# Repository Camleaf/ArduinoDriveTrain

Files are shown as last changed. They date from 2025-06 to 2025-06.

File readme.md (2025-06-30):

# Three wheel Crab drivetrain

**Description:** This robot can move in any direction without turning, using the Crab drive motion. It is controlled with the attached controller joysticks with the left joystick for arcade movement relative to the heading, and the right joystick to control the heading.

**Motivation:** I did this project because I wanted a challenge, also because I am looking towards joining an FRC team for the first time next year, and I wanted to make a drivetrain inspired by some robots I saw there. This project ended up taking less time than I anticipated (mostly because I was putting in 7-8 hour days on it), but it was still very fun.

**File Layout**:
 - **CAD**: contains the STEP files for the entire built, imports and all
 - **FIRMWARE**: contains all the code put on the microcontrollers
 - **WIRING**: Contains fritzing file, breadboard view and schematic view images, for both the controller and the car
 - **PRODUCTION**: Contains the individual .3mf files which will be 3D printed
 - **JOURNALIMG**: Where I store all the images I used for my journal

### Car Design Images

NOTE: The motors at the bottom of the design will get their power through wires from the motor drivers which are routed via the two big holes in each of the layers of design. Since to motors only move 90 degrees in either direction from their starting point in this design, the wires will never get tangled.

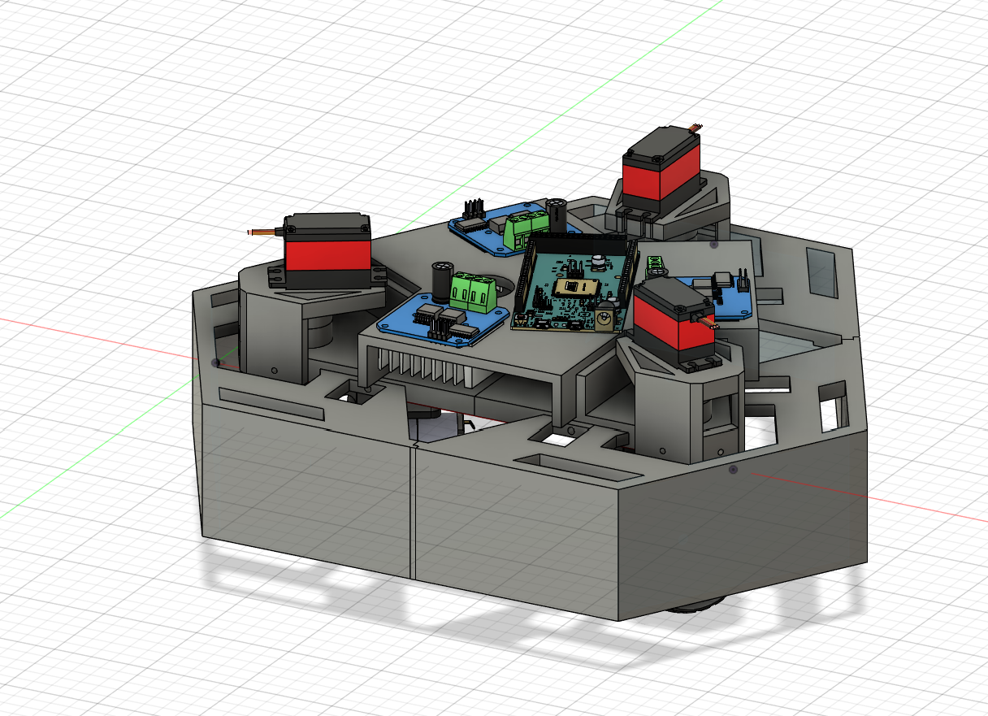
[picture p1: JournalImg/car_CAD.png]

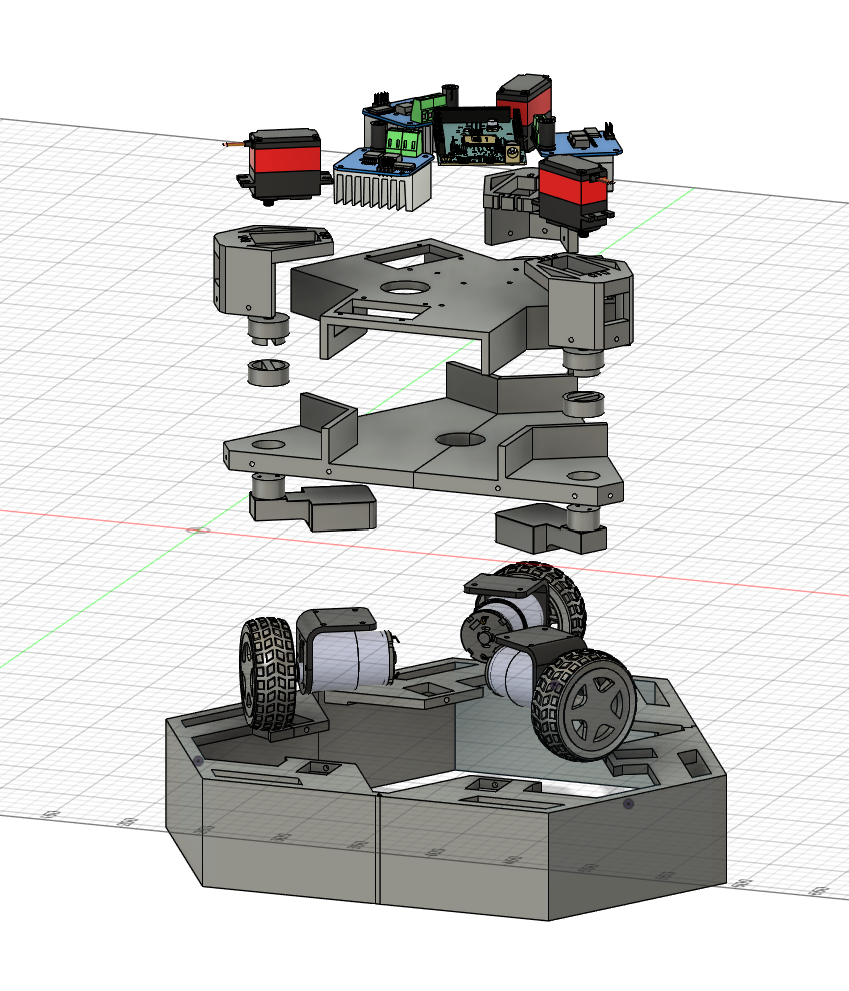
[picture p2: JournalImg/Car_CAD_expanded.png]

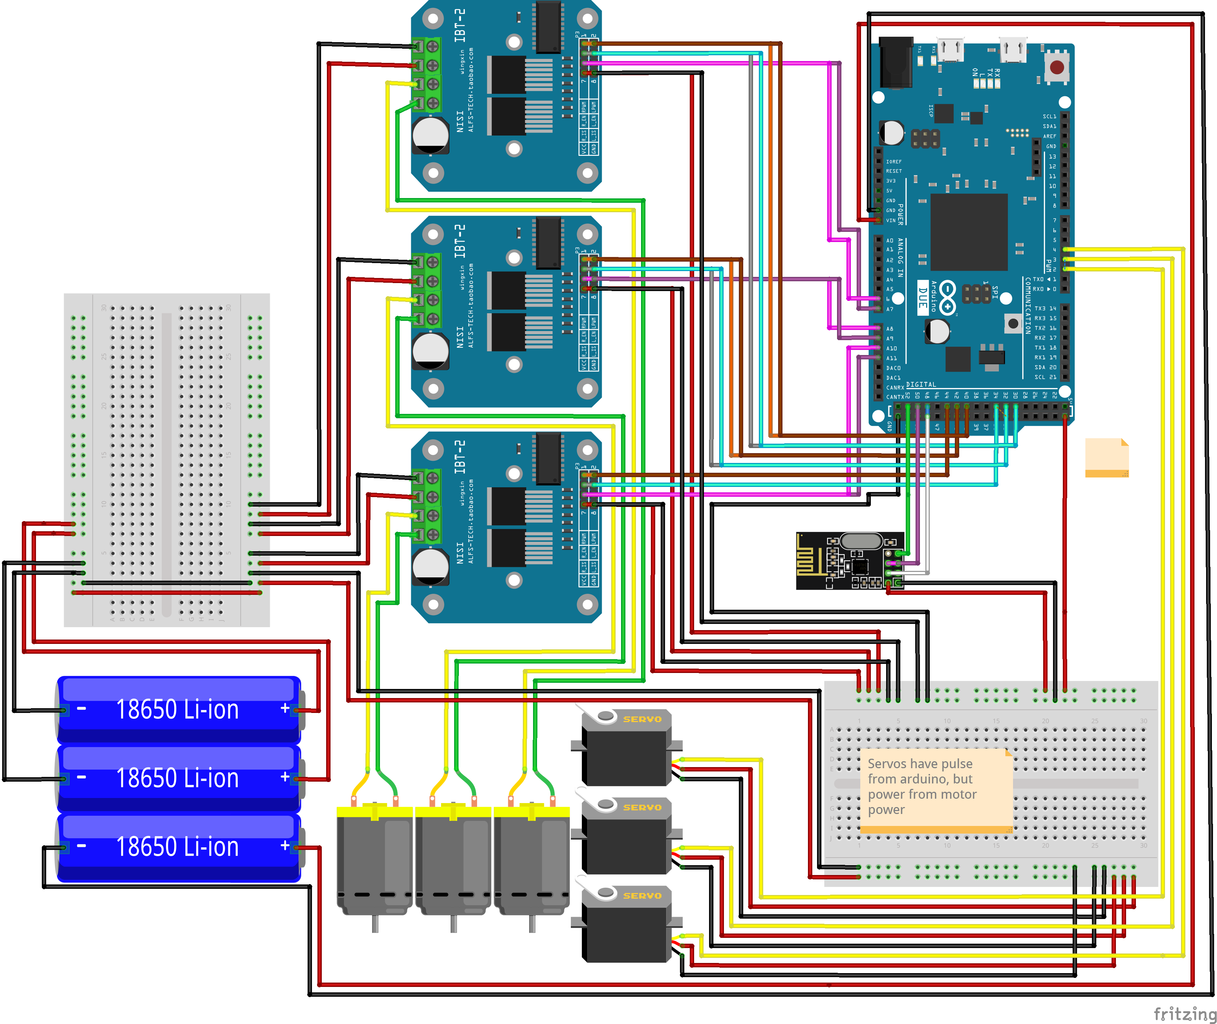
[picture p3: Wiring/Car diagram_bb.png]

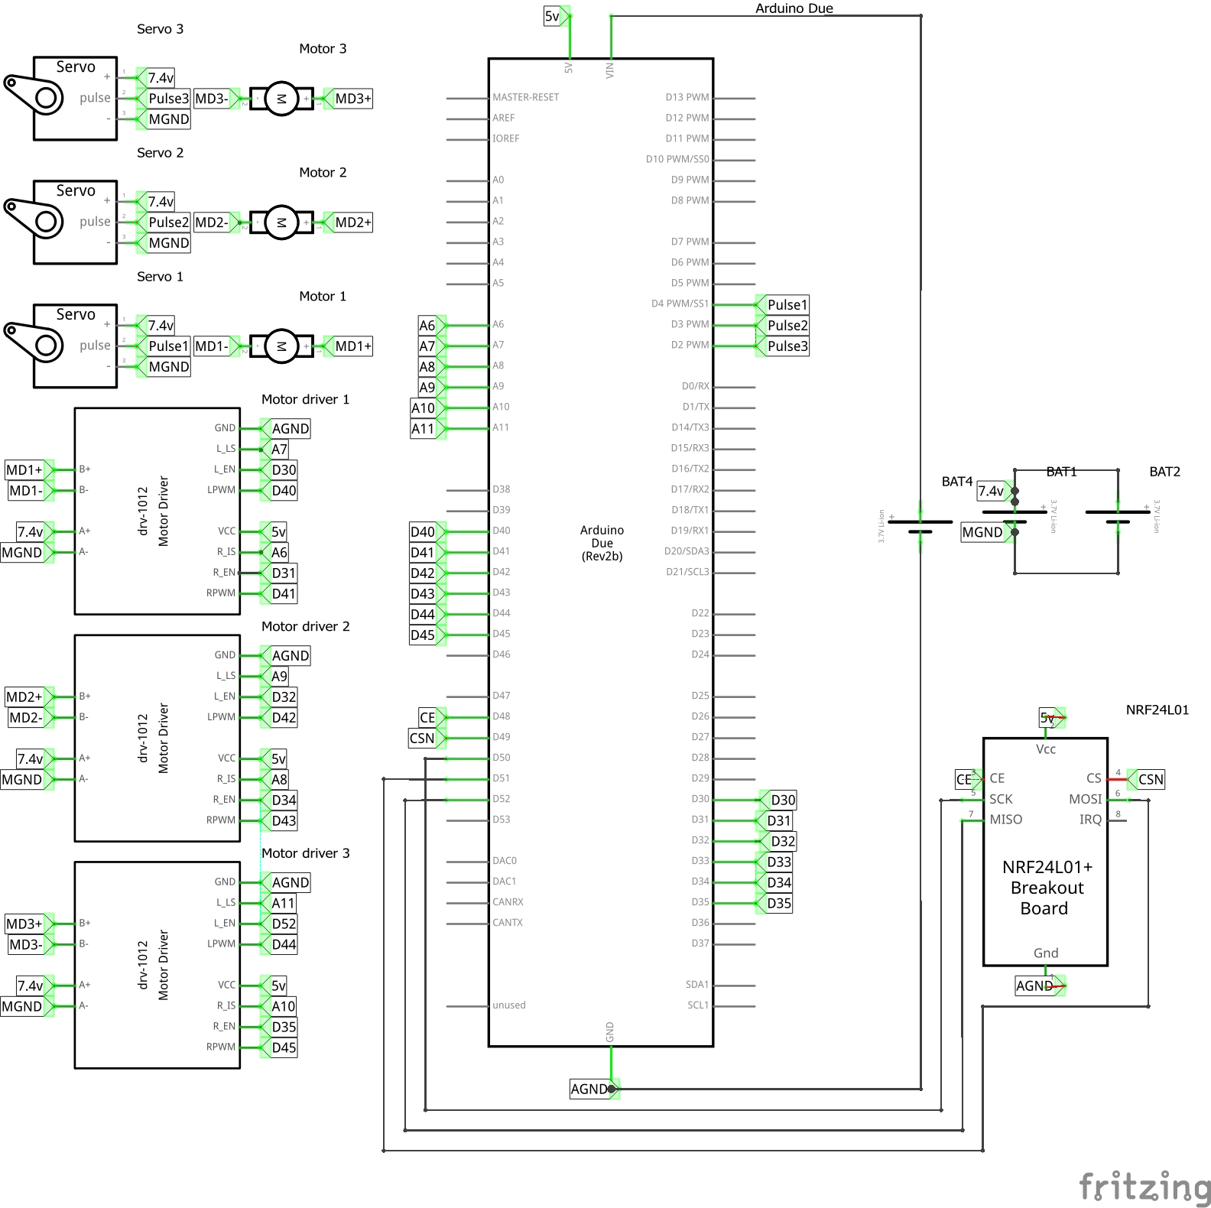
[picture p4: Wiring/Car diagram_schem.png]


### Controller Design Images

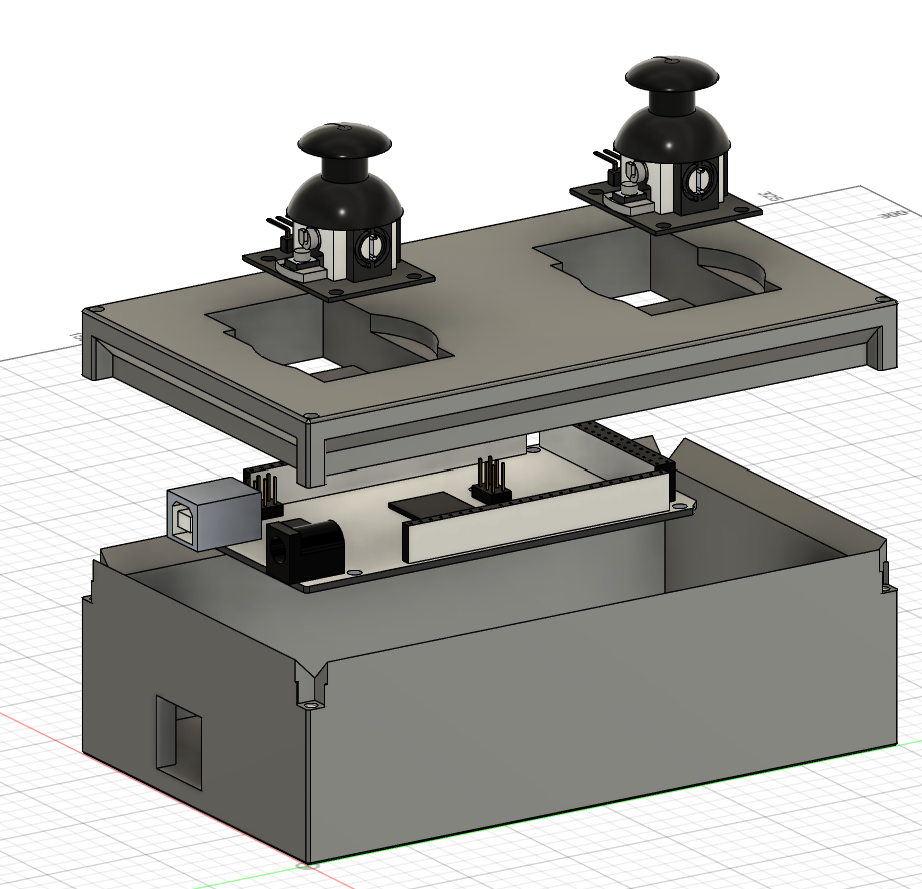
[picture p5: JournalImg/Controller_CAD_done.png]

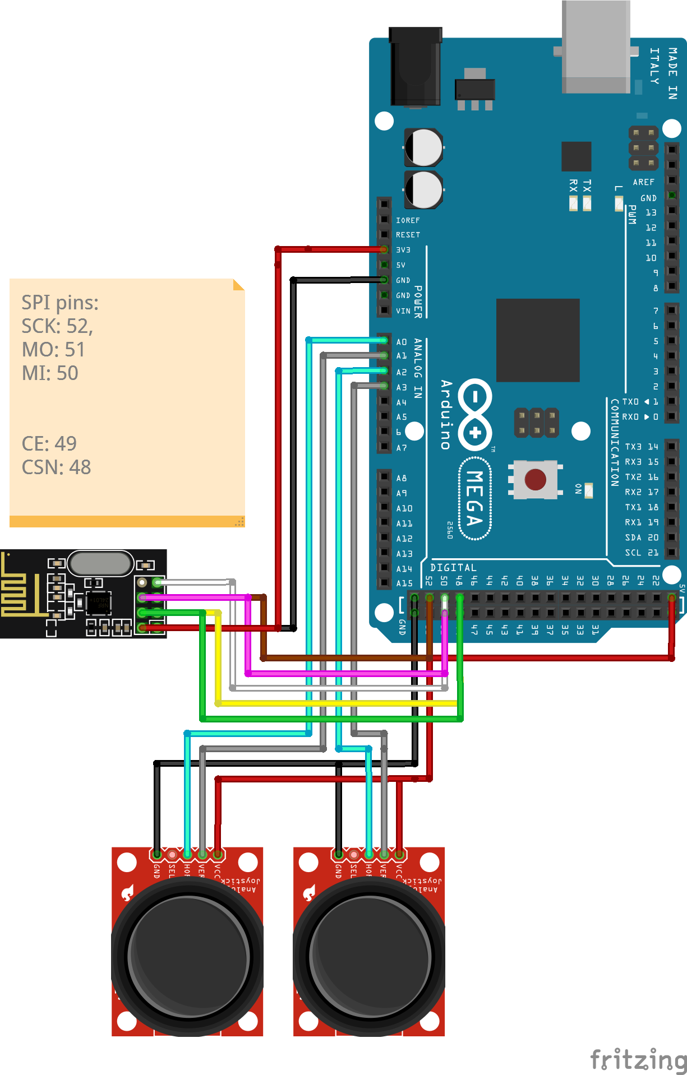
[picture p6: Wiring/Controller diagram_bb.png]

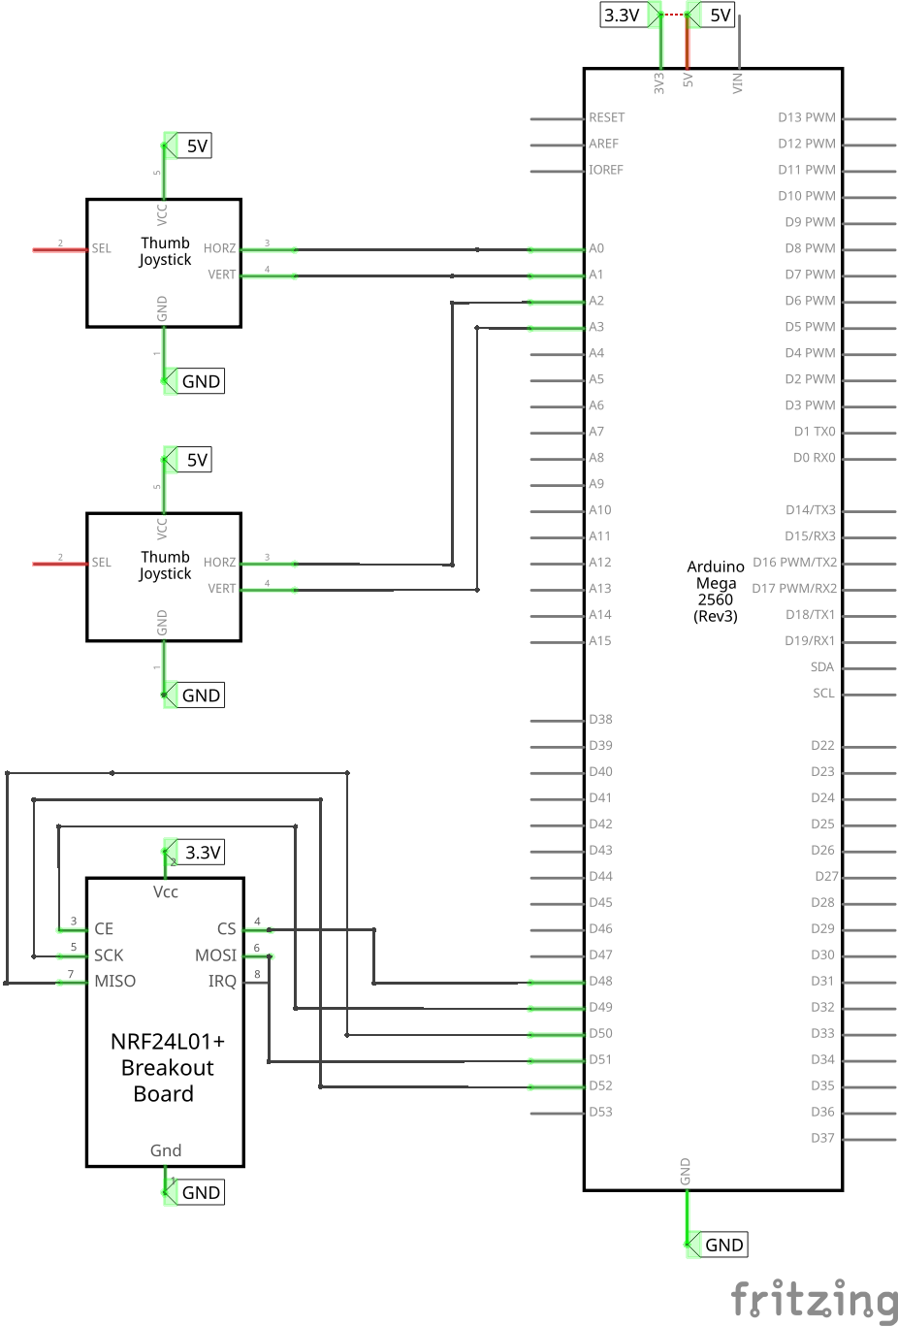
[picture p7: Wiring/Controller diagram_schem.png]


### BOM

I have a lot of parts at home and 3D printing capabilities so this list is just what I don't have.

|Item #|Name |Quantity|Type |Description |Cost |Link |FIELD8|FIELD9|FIELD10|
|---|---|---|---|---|-----|---|---|---|---|
|1 |BTS7960 |2 |2pcs |Motor Driver |6.04 |https://www.aliexpress.com/item/1005006795884033.html?spm=a2g0o.cart.0.0.37ee38dastskZr&mp=1 | | | |
|2 |XY joystick |1 |5pcs |Joystick for controller |3.21 |https://www.aliexpress.com/item/1005009059629265.html?spm=a2g0o.cart.0.0.37ee38dastskZr&mp=1 | | | |
|3 |7.4v 1500mAh battery pack|1 |3pcs charger |Powers motors/servos |11.29|https://www.aliexpress.com/item/1005007104046547.html?spm=a2g0o.cart.0.0.37ee38dastskZr&mp=1 | | | |
|4 |JGB37 DC motor |4 |6V bracket motor|main motors |16.63|https://www.aliexpress.com/item/1005009003269281.html?spm=a2g0o.cart.0.0.37ee38dastskZr&mp=1 | | | |
|5 |Arduino Mega |1 |official-cable  |microprocessor |12.99|https://www.aliexpress.com/item/1005006661386732.html?spm=a2g0o.cart.0.0.37ee38dastskZr&mp=1 | | | |
|6 |JX PDI-6221mg servos |1 |4pc |servos to rotate motor  |16.63|https://www.aliexpress.com/item/32880168203.html?spm=a2g0o.cart.0.0.37ee38dastskZr&mp=1 | | | |
|7 |USB power bank |1 |1pc |Power for microprocessor|10.71|https://www.aliexpress.com/item/1005008829680504.html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| | | |
| |Shipping |N/A |N/A |N/A |36.47| |

Total: $129.92 USD

With tax: $146.8096 USD

This is with Aliexpress First time shopper welcome sales, as I have never shopped there before.
The previous total was ~$180. Good thing those exist so I could get under the limit.

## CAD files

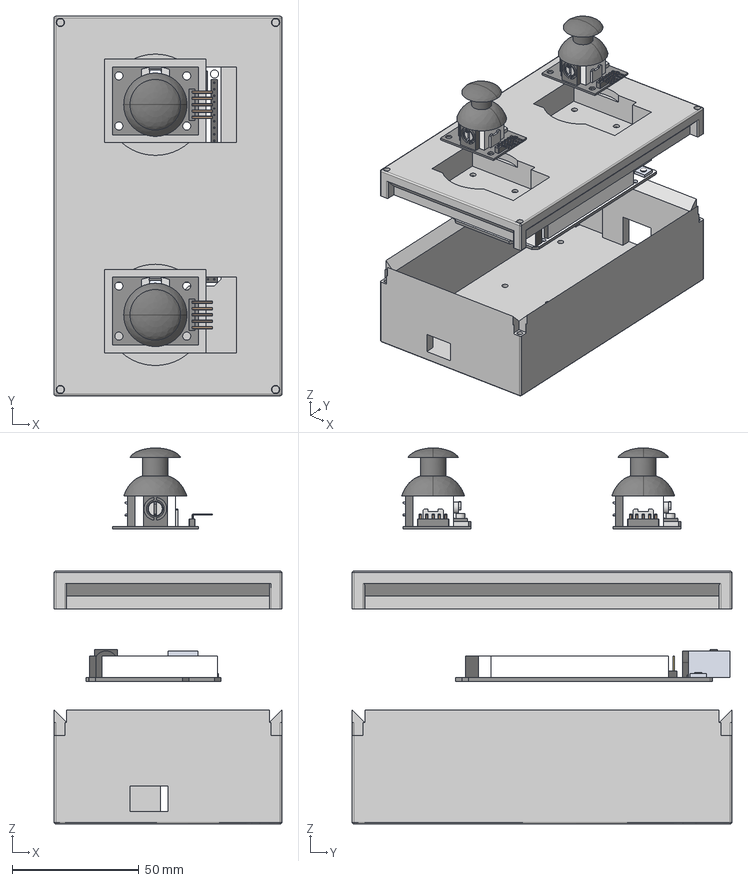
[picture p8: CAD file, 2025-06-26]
CAD/Controller.step
90.0 x 150.0 x 148.5 mm
Joystick HW504 Board.SLDPRT x 2

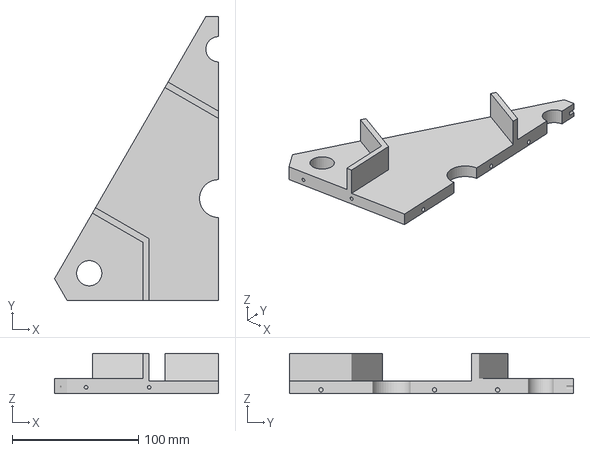
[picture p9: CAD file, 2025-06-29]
Production/Half 1.3mf
130.0 x 225.2 x 32.0 mm

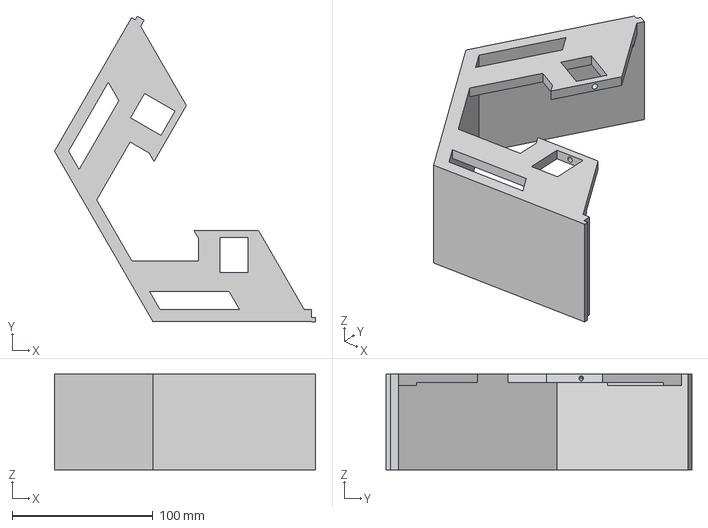
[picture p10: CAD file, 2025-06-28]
Production/Motor Shield.3mf
185.5 x 217.2 x 68.0 mm

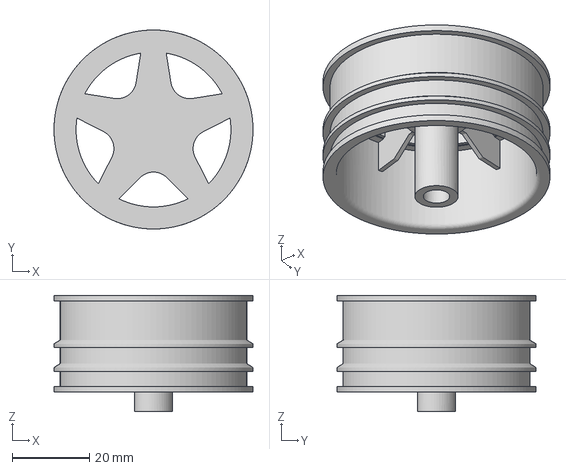
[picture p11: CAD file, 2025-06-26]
Production/WheelBody.3mf
51.4 x 51.4 x 30.0 mm

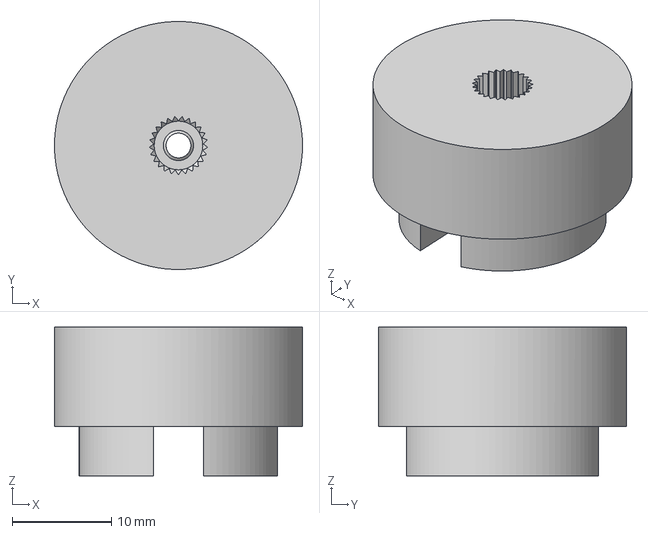
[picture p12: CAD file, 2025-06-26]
Production/Servokeycap.3mf
25.0 x 25.0 x 15.0 mm

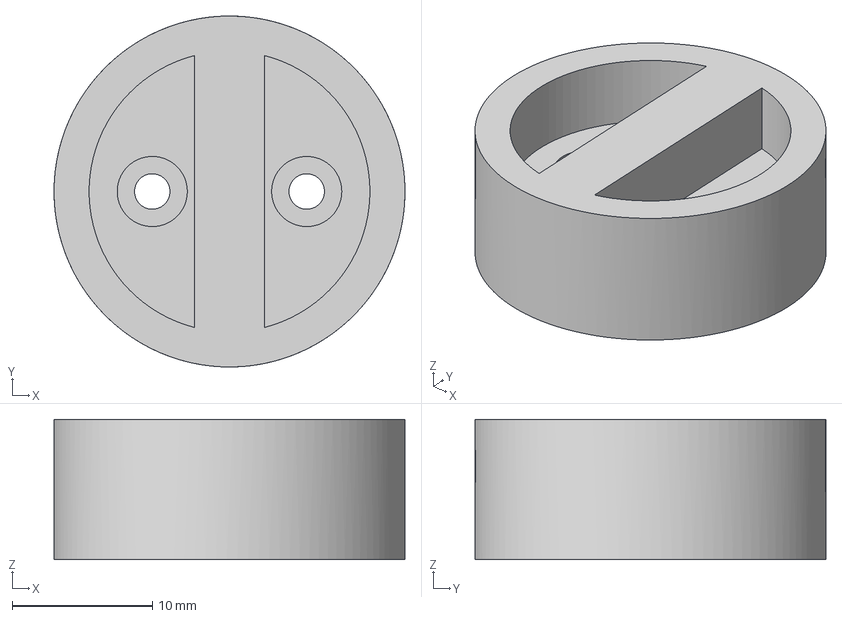
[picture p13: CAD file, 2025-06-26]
Production/Keycap.3mf
25.0 x 25.0 x 10.0 mm

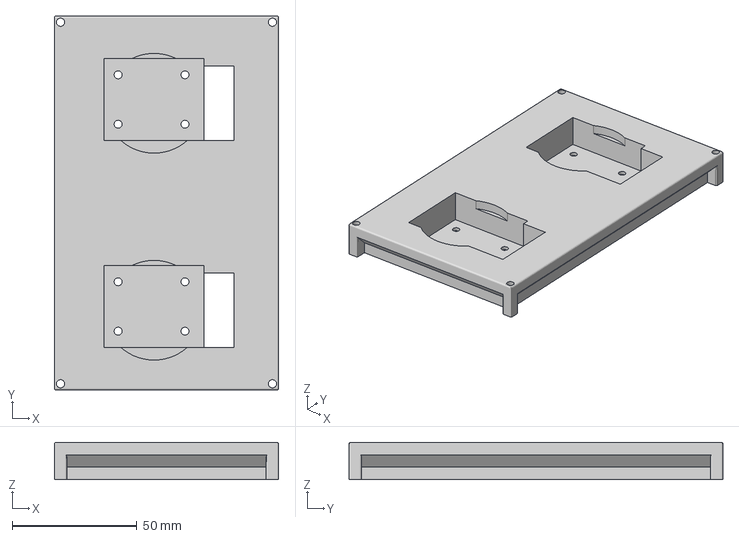
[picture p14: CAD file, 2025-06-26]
Production/Controller Top.3mf
90.0 x 150.0 x 15.0 mm

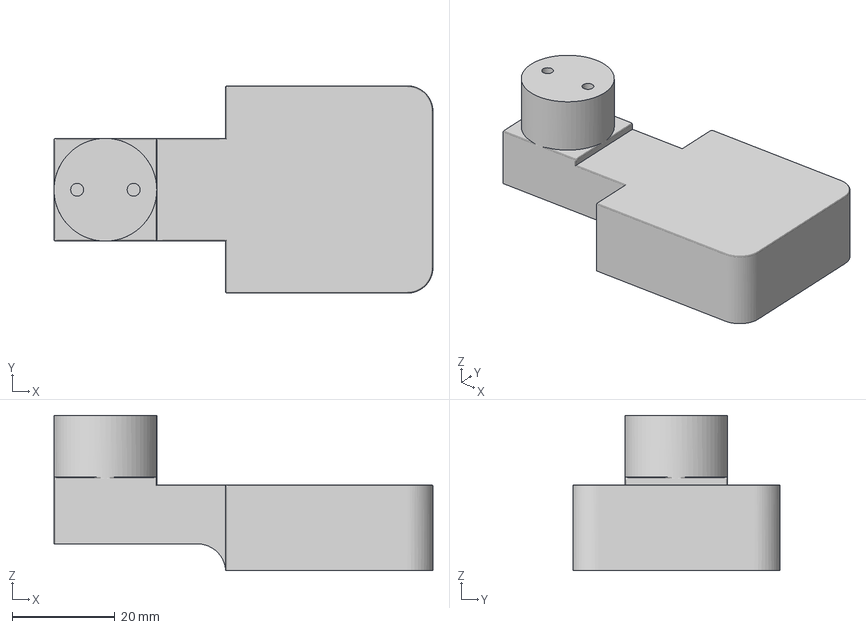
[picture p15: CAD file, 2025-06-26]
Production/Motor holder.3mf
73.8 x 40.3 x 30.2 mm

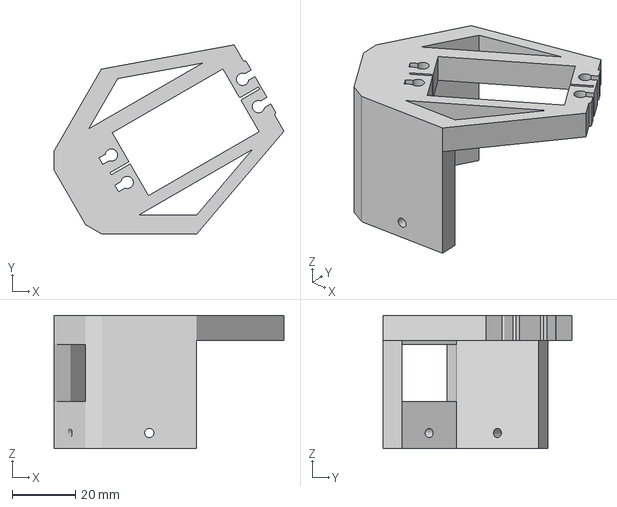
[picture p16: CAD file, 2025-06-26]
Production/Servo holder.3mf
72.9 x 60.0 x 42.3 mm

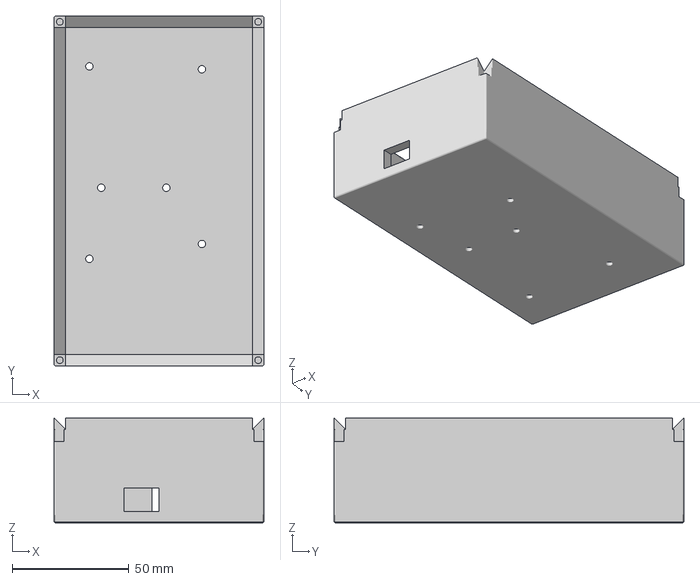
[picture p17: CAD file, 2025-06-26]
Production/Controller base.3mf
90.0 x 150.0 x 45.0 mm

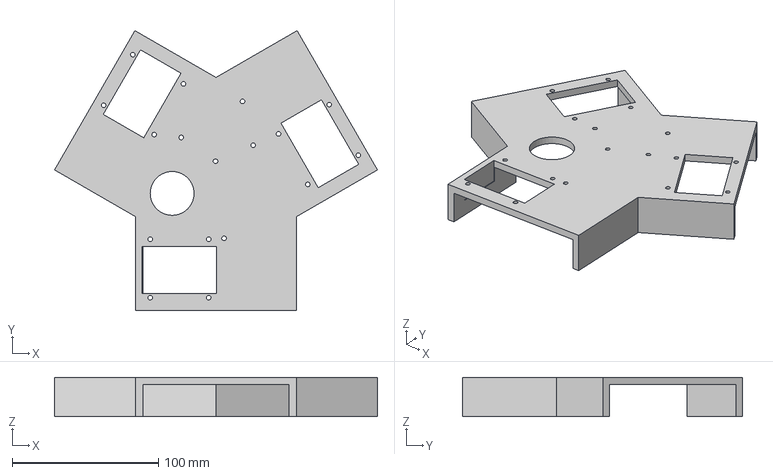
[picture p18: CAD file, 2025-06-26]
Production/Body Top.3mf
221.0 x 191.4 x 27.0 mm

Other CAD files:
Production/Half 2.3mf

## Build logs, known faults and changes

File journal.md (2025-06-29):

---
title: "Tri-wheel Crab Drive"
author: "Camleaf"
description: "A Crab drive rc car, fully 3D printed frame"
created_at: "2025-06-22"
---
**Total Time Spent: 35.5h**

The initial goal for this project is a full tri-wheel car with holonomic motion. The goal is to make two drive modes: Ocelot and Crab. Ocelot is field-centric, and has full holonomic motion, however will likely require magnometer/gyro configuration and is considerably complex. Crab is car-centric, meaning it skips any magnometer/gyro configuration, and it can be a nice fallback if those components fail. It can still move in any direction, however motion is not fully holonomic.

# June 22th: Did some research on ordered parts

I had a version of this project on the backburner last year, and It came to a grinding halt as I had no budget and I realized the parts I had didn't fit my goal.
Since then the entire project has been lost somewhere on an old hard drive (probably in my shed), and I thought that now would be a great time to pick it back up!

Today, I didn't start too much with engineering, instead I look and found some pieces online which I believe at this moment will fit my purpose.

A 20kg 0.10s/60deg servo
 - I have some old 10kg servos but they struggled a lot on the old version of this project, so I'm bumping up. These are also ridiculously cheap for some reason
A N20 500rpm geared motor
 - My last motors were standard TT gearbox motors, and I think these are a good step up in speed and handling
 
At the moment no photos because they are all still online, however this research did take me some time. 
It is very preliminary so things probably will change

**Total time spent: 1.5h**

# June 23th

#### Budget update info
At the start, I updated my budget, as I realized that the 150 budget was in USD instead of CAD. I also moved a lot of my items to AliExpress because it is a lot cheaper
As a result of this I was also able to fit an Arduino Mega on the budget, with an additional $30 left (Needed because I need the floating point operations to be fast, also I am comfortable with arduino).
<br>
<br>
#### Modify standard TT wheel design

I also started a decent 3D model, and imported the motors/servos into my 3D model to start modeling around.

I realized that the default Arduino TT wheel model (yellow wheel) didn't have a matching attachment point for the motor to the ones I am planning on using, so I changed that and sent a model out to 3D print from PETG (grey). I'm happy how it turned out.
The 3D model with the new motor is pictured on the right.


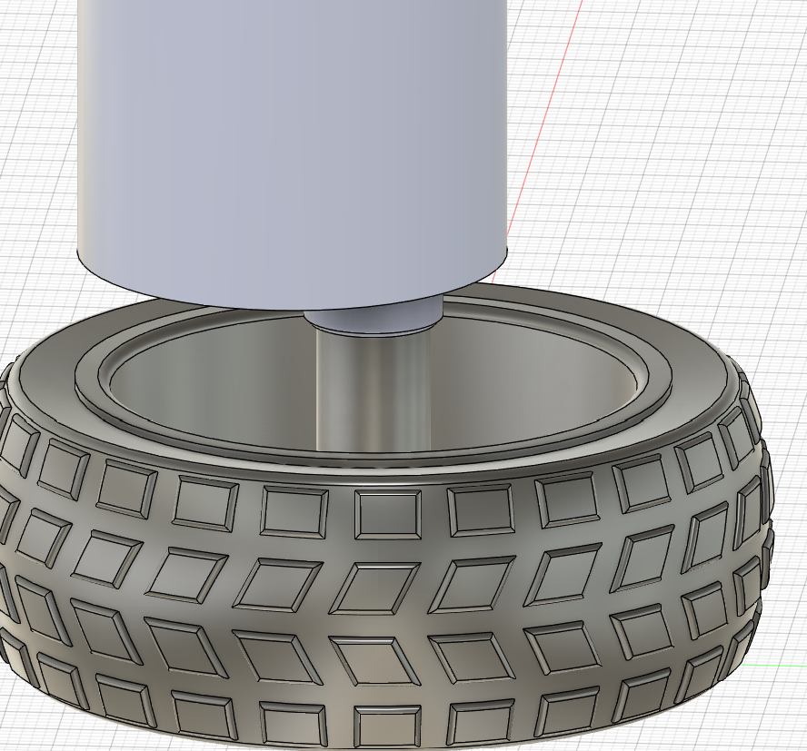
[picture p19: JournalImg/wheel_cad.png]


Seeing as it works suitably as a replacement, I'm going to now pivot towards the frame of the car
<br>
<br>

#### Car frame

The best shape for a tri-wheel swerve drive, as it has the most stability parity in every direction

I created a new document, and made sketch of equilateral triangle with 250 edge length, then put some holes in for the modules to go.

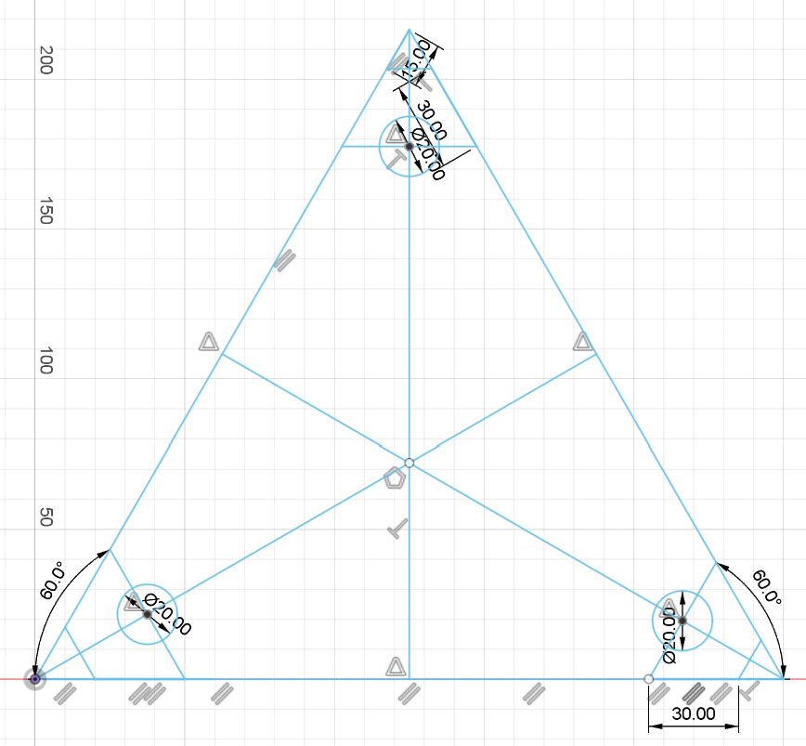
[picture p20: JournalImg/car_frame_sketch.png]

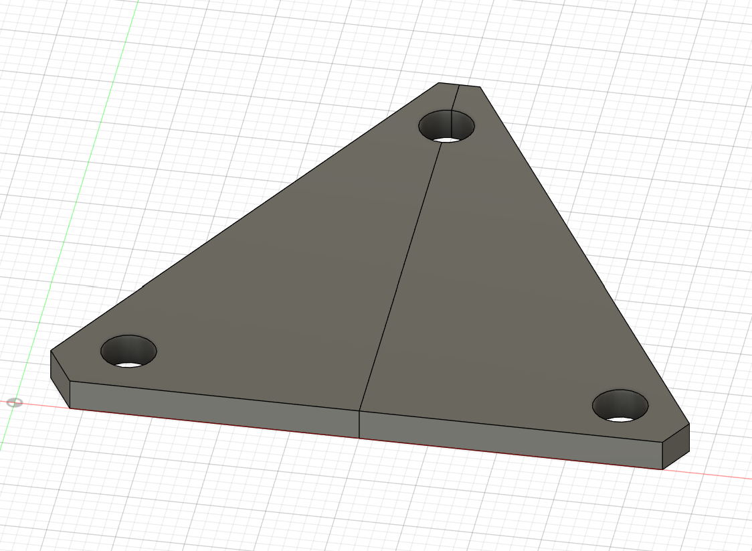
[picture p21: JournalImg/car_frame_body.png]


The wheel modules are equidistant from the center and their respective corners, and are on the medians. They should be in a close enough spot to the edge to keep stability and to allow space for other components

<br>
<br>

#### Wheel rotator module

I then started to build a crab drive module in CAD.

Based on previous experiences trying and failing to make this, I know that the module needed to be:

 1. IT NEEDS TO BE SIMPLE: overcomplicating things leads to easily breakable parts, which isn't good for reliability. 
 2. Wheel needs to stay in the centre, and the servo needs to be directly over the wheel: This isn't really from any previous experience, just something I thought of while making the model to help with the rotation coding later on. It also does mean that the connection from the servo to the motor needs to be a kind of L-shape though

Ok, after a few hours, I came up with this preliminary design:

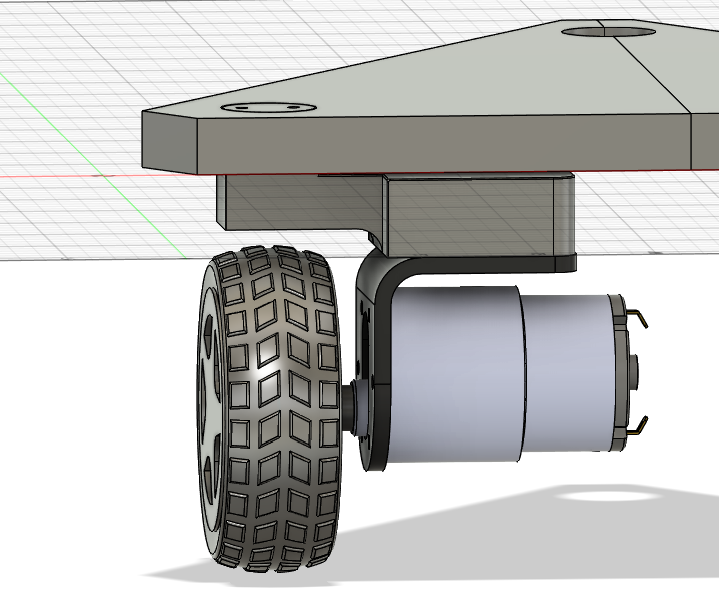
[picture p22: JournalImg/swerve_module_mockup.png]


It has a few issues, for example the possibility of friction between the base and the module, and the fact that if this module does a full spin, then the wires will get caught. I think that these issues can be resolved in time, but for tonight I've done a lot of work and am tired.

**Total time spent: 4h**

# June 24th: Cadding away
A tentative 3D print of the base (pictured left), made me realize that I forgot a connection mechanism between the two halves of the base ( two halves because my 3D printer isn't big enough), so I went and added it in CAD (pictured right)


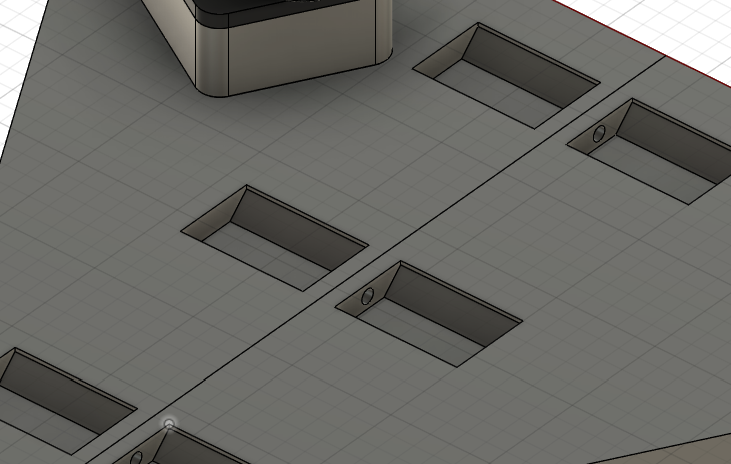
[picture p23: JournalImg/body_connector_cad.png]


#### Wheel rotator

I finished the initial design of the wheel rotator module, and I created a raised platform for the rest of the car

For the wheel rotator module, I added a connector piece to connect the servo and the rest of the module

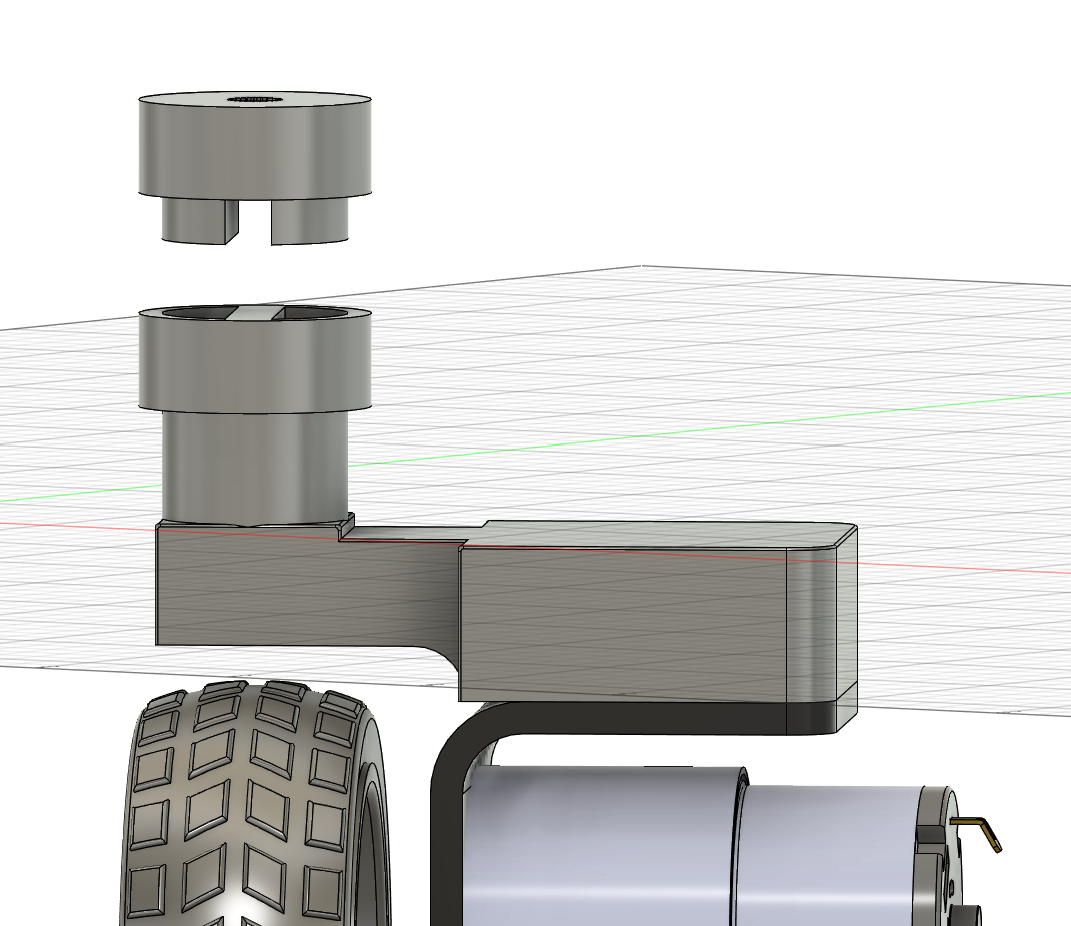
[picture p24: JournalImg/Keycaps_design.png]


The plug shape of the connector should be a sturdy fit when rotating

Then, I created this piece to attach the servo to the base frame. I then did a 3D print of it and I haven't been able to bend it easily, so I think it is a solid design.

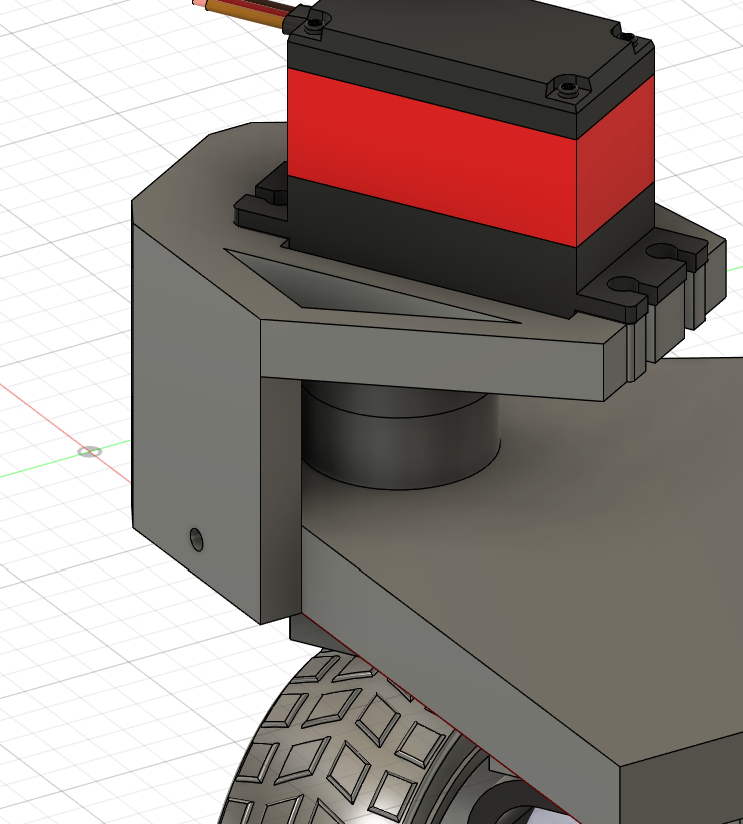
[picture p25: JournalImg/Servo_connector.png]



One struggle i had with this was finding an appropriate JX PDI-6221MG servo model to base my designs off of, but luckily grabcad had one [here](https://grabcad.com/library/jx-pdi-6221mg-servo-180-1). I checked its measurements against those on the manufacturers website and the measurements lined up.

Unfortunately, this module made it so that screws had only a very limited space to be put, lest they interrupt the wheel/motors rotation path.

#### Frame raise

Because of that, I decided to raise part of the frame. This sketch details what is going to be raised (blue), and what is part of the motor apparatus (grey). I then extruded it to add space for the screws. Raised, pictured right, sketch, pictured left.

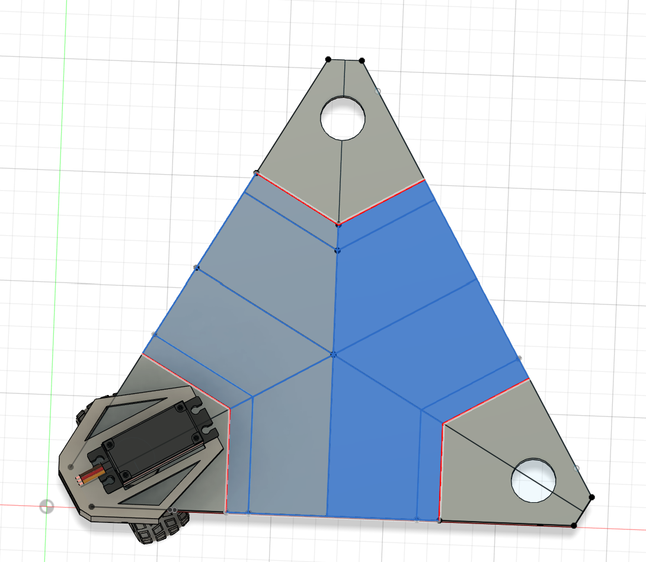
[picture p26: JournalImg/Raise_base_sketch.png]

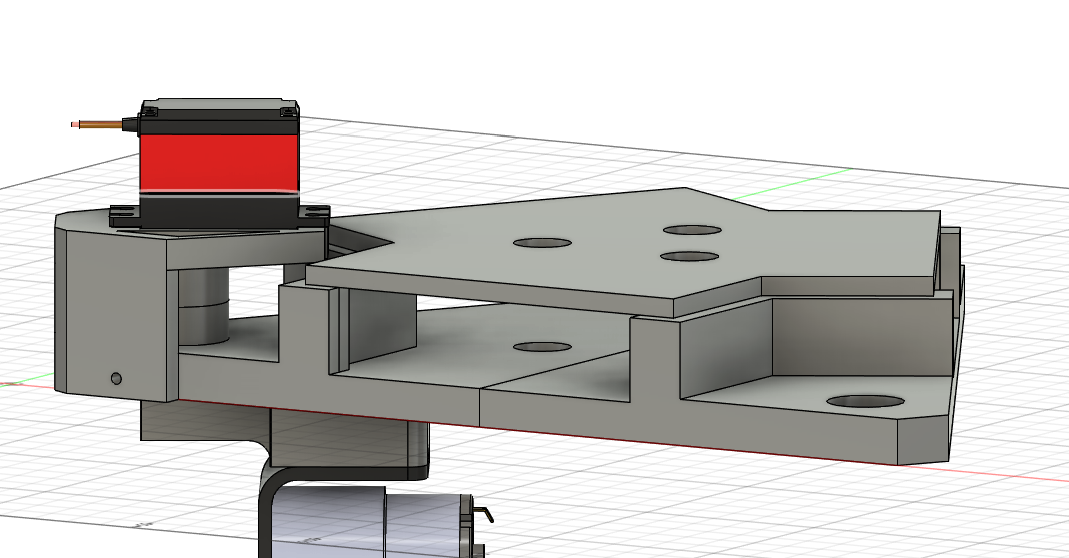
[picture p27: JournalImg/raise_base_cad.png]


The raised section on the right side is a separate component for 3D printing purposes.
It should slide in to the main section with no screws (tolerance of 0.1mm).

**Total time spent: 6h**
<br> ^ It's  summer, alright, don't judge the insane hours

# June 25th: Working on the raised section

I found a severe issue with the raised section: It doesn't fix the issue I had:

I thought that I would be able to put the Arduino on the top half, and the motor drivers (BTS7960) /batteries on the bottom half, but as it turns out, the motor drivers interfere with the pins which attach the frame together, so I can't place them on the bottom, this means thatI am back where I started in terms of placement. (left)

I fixed it by expanding the center section out on the sides, and the piece should still fit onto my 3D printer. (right)

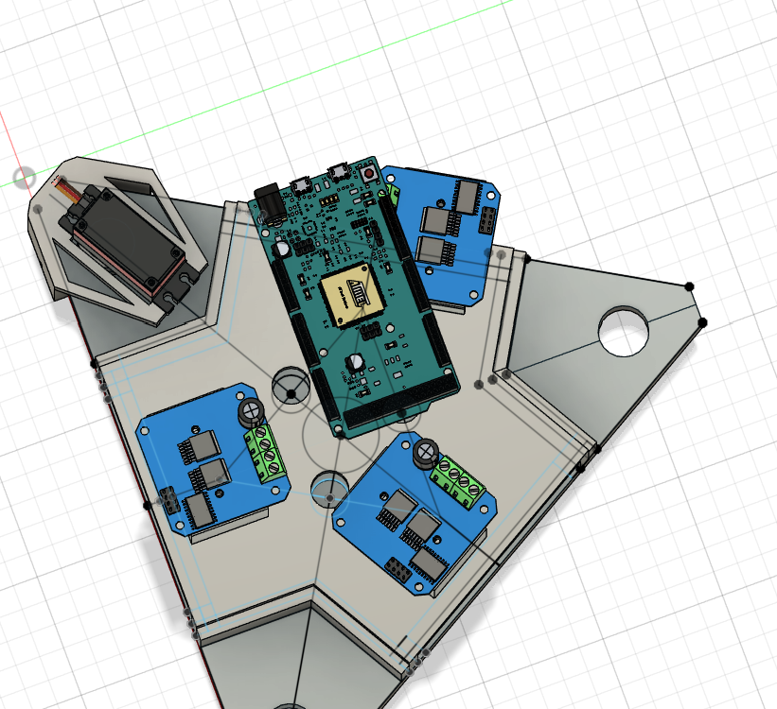
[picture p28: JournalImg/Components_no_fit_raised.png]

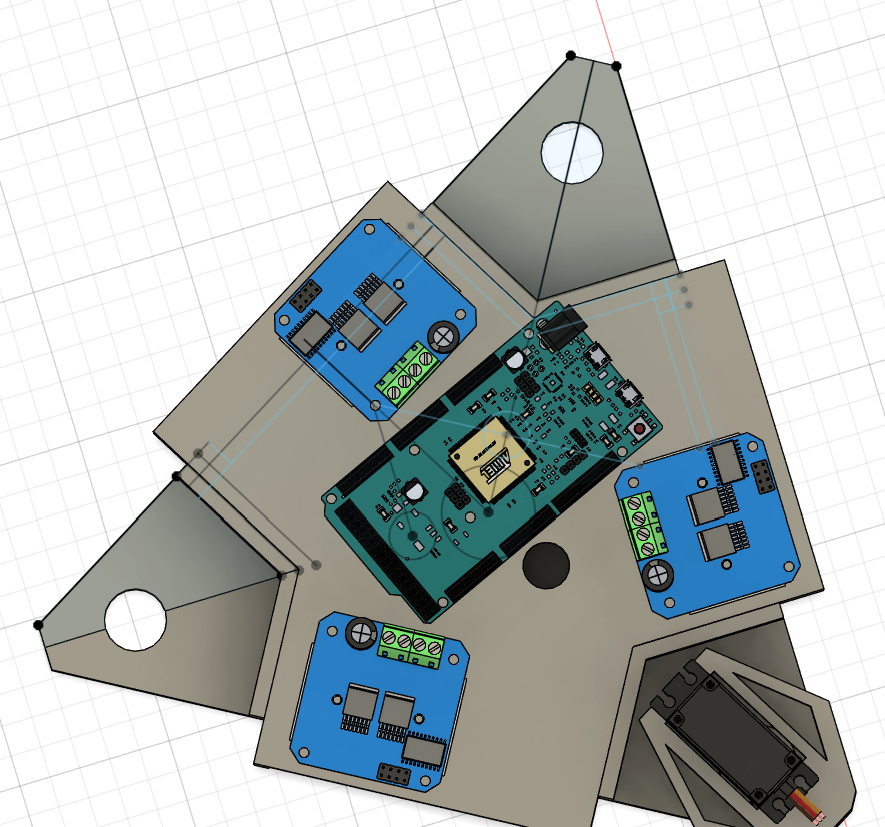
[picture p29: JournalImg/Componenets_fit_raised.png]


<br>
<br>

#### Updating goals

I still think that full field-centric holonomic motion for this bot would be really cool, I would need a magnometer, which while inside my budget, has a level of complexity involved in the calibration/operation that I can't seem to wrap my head around. Also, this saves me from having to CAD in another raised platform to minimize hard iron distortions. I will from here scrap my idea of having multiple drive modes and focus solely on Crab drive, where you can move in all directions but it is robot-centric.

With that, however, I believe that this part of the CAD process done. Now I can move on to circuit diagrams and programming.




 I will need to go back to 3D modelling for the controller, but I think I'll take this one step at a time

### Circuits

The process of creating the circuit for what I need shouldn't be too difficult. All I need to do should be:

- Boot up Fritzing ( The circuit software I'm using, I will ignore the PCB section as I am not creating any)
- Add the Arduino Due, NRF24L01 (which I'm using for radio), 3 BTS7960 motor drivers, 3 servos, and 3 dc motors (I can use generic ones here because the inputs are the same)
- Connect all the wires to their appropraite handlers: 5v + arduino handles logic, 7.4V supply handles power

Unfortunately given that the BTS7960 isn't built in to Fritzing, I had to look for a user-made one, and the only one I could find couldn't be run in the Fritzing circuit simulator, so I'm going to have to wait to test this circuit once I have the pieces.

Also, I couldn't find the models of battery packs I am planning on using, so I just put placeholder 18650s in their place, seeing as this circuit wasn't going to be run anyways




The wiring went mostly without a hitch, and I connected everything and then verified the connections to make sure nothing was off. The only thing that bothers me is the fact that on the built-in Arduino Due module, the usb-b mini ports and the SPI pins weren't added into the module, so I couldn't plug those pins in. However, I left a note to remind myself and any potential readers, so It should work just fine.

I honestly wish that something went wrong during this process, or that is was more complicated, because I think I spent the last four to five hours mindlessly connecting everything.

I think that tomorrow I should start working on the controller.
I'm getting the feeling that the planning stages (before I get the grant) of this project will be over a lot faster than I'm expecting because of the insane hours I'm putting in.

**Total time spent: 7h**

# June 26th: The controller

#### Cad

I started the measurements for my controller around an arduino mega, because it is a good size to start to model something ergonomic around, and I happen to have one laying around, so there is no point buying something new.

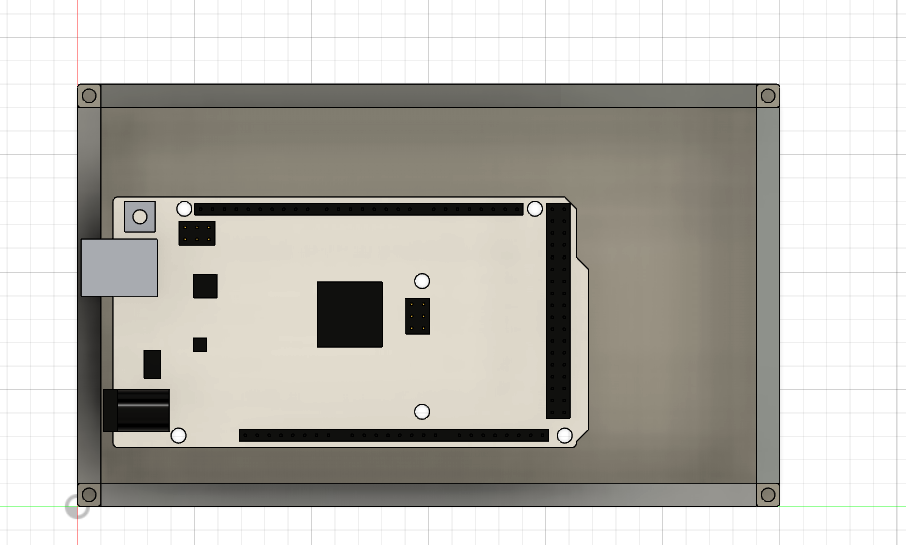
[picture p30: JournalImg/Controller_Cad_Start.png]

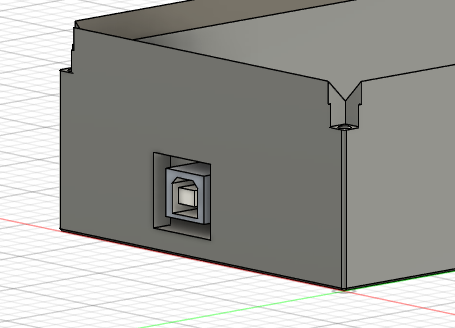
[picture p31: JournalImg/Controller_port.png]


I think It turned out well, and I added a little IO on the controller to connect it to my computer, removing the need for a battery for this.

From there, I designed a little top hatch which fits perfectly onto the base, and can hold some HW-504 joysticks. I also left a bit of space for a rf24 radio module



The CAD for the controller was extremely simple compared to that of the car. I'm sure I will eventually make changes once I feel it in my hands, but at the moment I'm out of printer filament so I will need to get some more before I can hands-on test.

#### Circuit

The circuits for this were relatively easy compared to the car, as all I had to do was connect SPI pins to the NRF24l01 module, and connect the analog pins and power to the joysticks.




After this, I wrote the Readme.md and compiled all the external items I need into a BOM.csv, which took about an hour and a half

I also realized at this point that although the Arduino Due is a lot faster than the Arduino Mega, the fact that it runs mostly 3.3v instead of 5v is a dealbreaker for me, so I am going to switch it on my BOM, however since it has exactly the same pin locations and footprint, I can leave the CAD and circuit designs intact and drop in the Mega on my real project.

#### Drive control

I realized that now that I'm done wiring and CAD for everything else, I needed (and still need to) figure out the maths behind the drive mode
So far I realized that I will need the rotation and force from both the joysticks, so I drew up a diagram for that, but am still coming up with the car drive stuff.

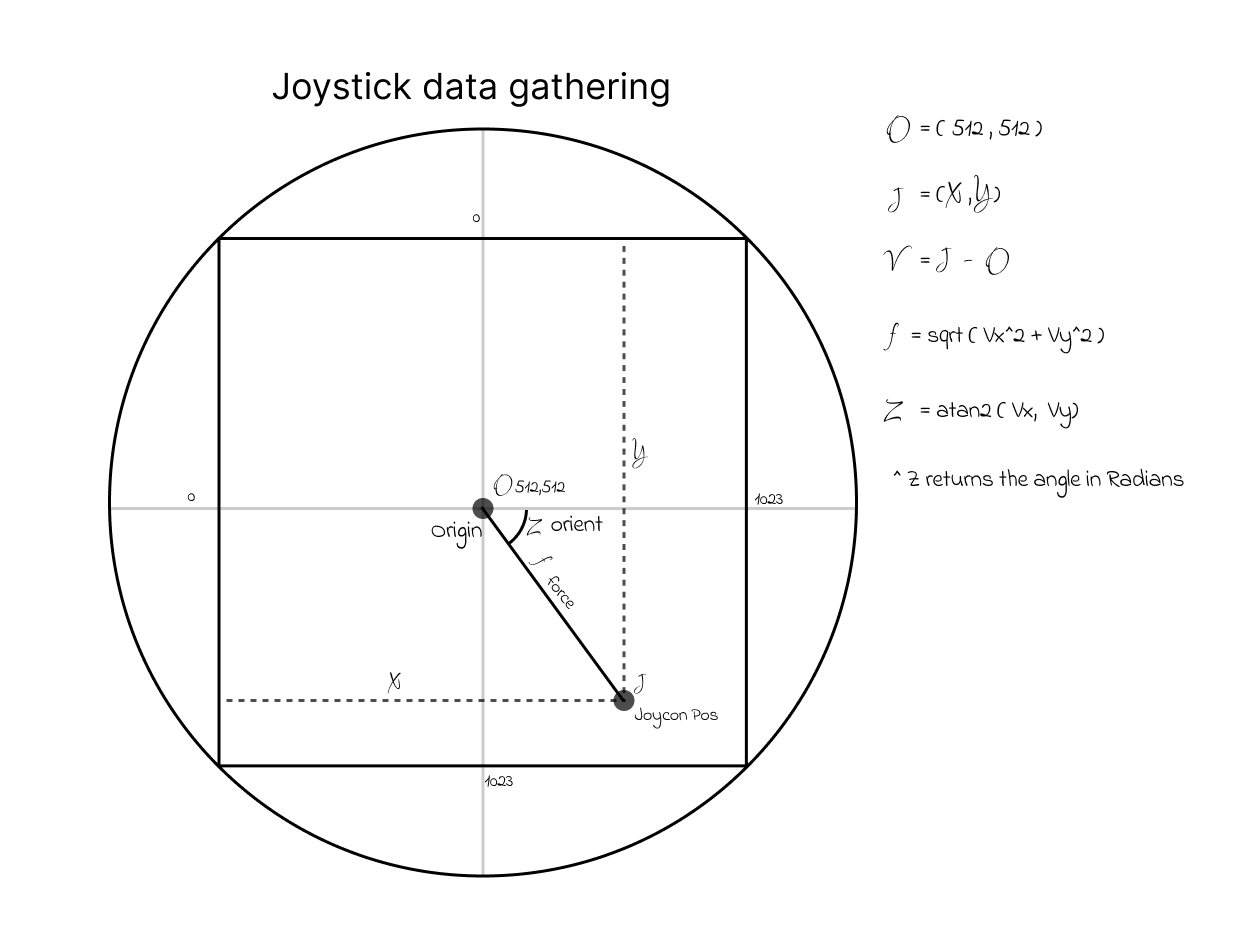
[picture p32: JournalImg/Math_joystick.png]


Using the input only from the left joystick (movement + force), and NOT the right joystick (rotation), I came up for this movement chart for when the robot is not turning.

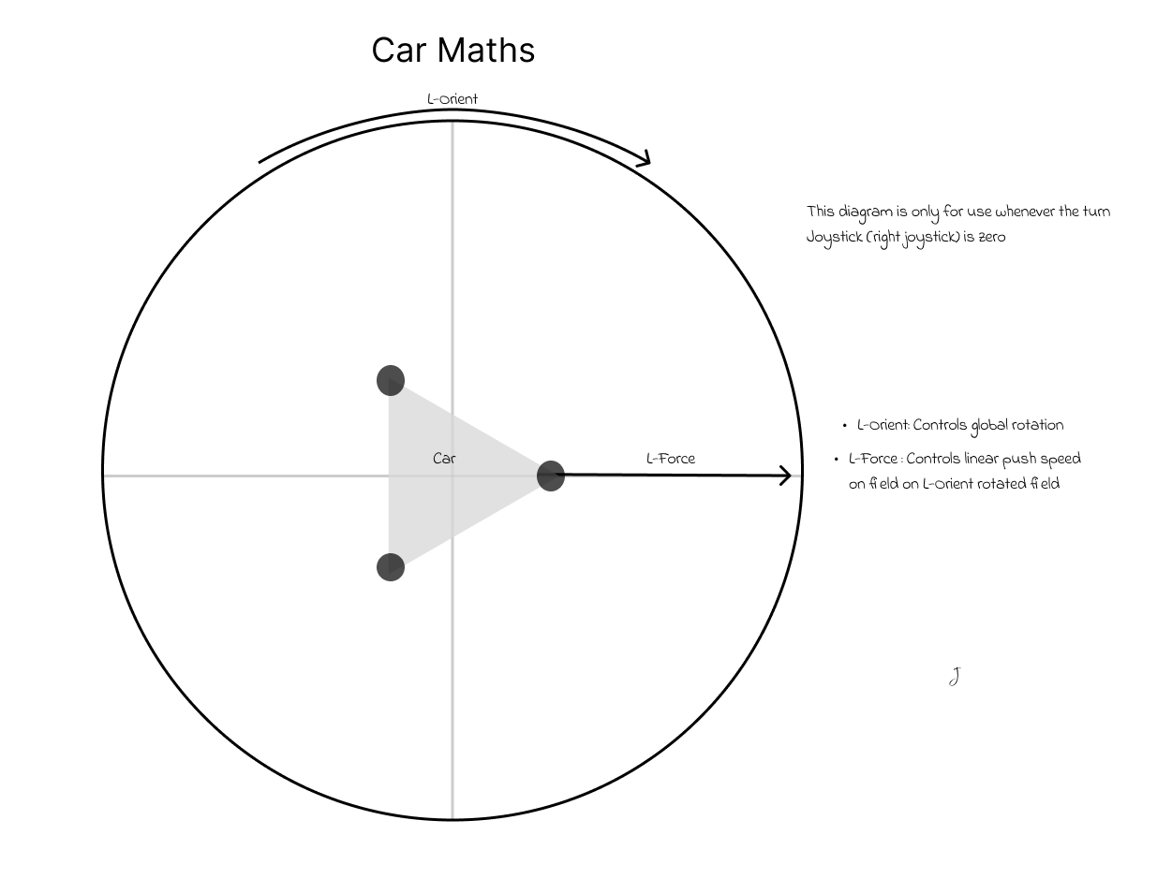
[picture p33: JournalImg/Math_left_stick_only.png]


Now that the case for only left joystick use has been solved, it is time to look at the more general case of the right joystick being moved. The first step in this process is to find the rotation point that the robot is to rotate around, likely outside of the car. This diagram details the process of finding that point with regard to the data given by Joystick data gathering.

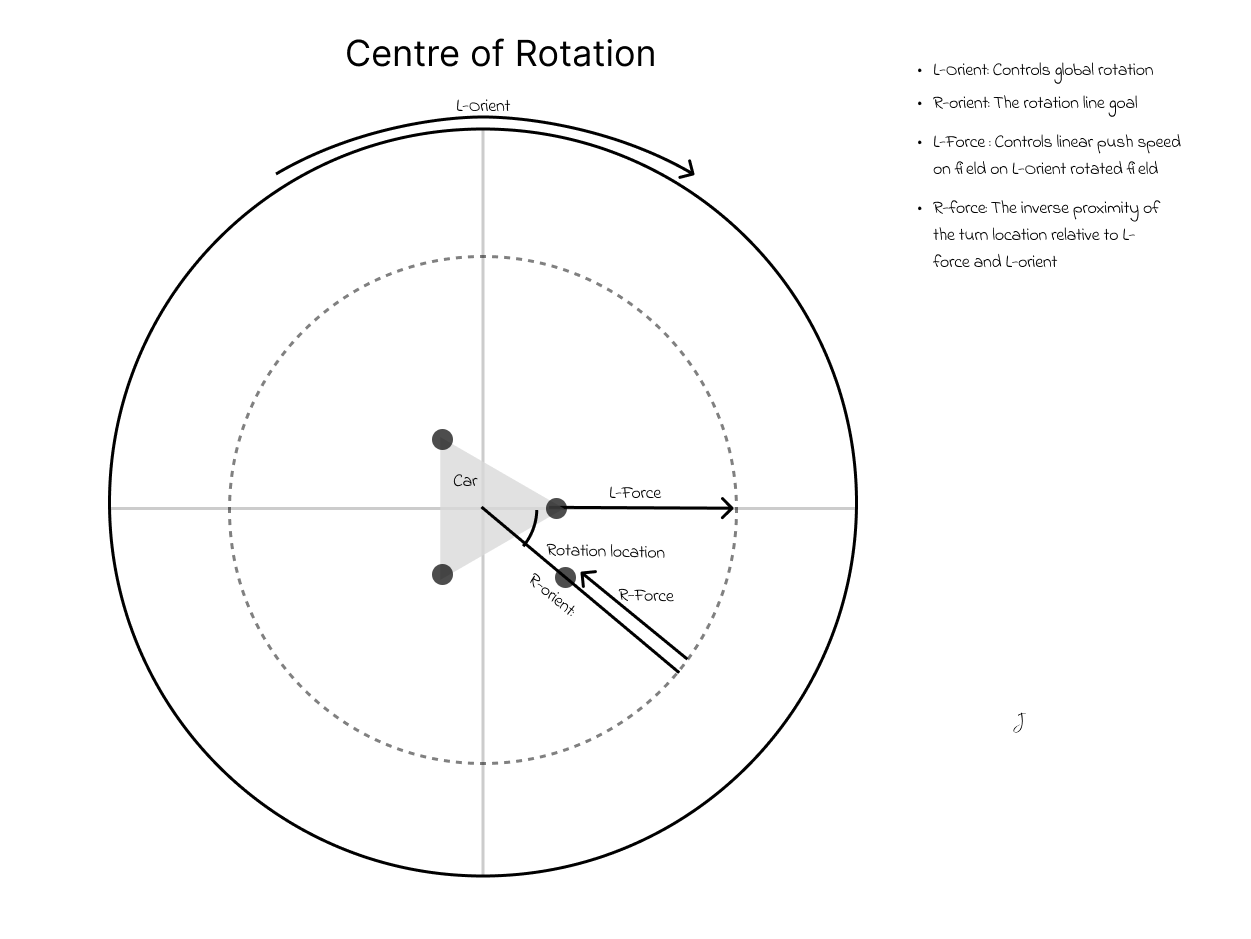
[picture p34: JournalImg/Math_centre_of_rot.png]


**Total time spent: 8h**

# June 27th: More math and some coding

I started to build some transmitter code based off of my diagrams, my wiring plans and the CAD software. It uses the RF24 library and went mostly without a hitch. Unfortunately I will have to wait until I get the parts to test, however the code looks good.

Also, I built the basic Crab drive math without turning (2nd geometry diagram above) into my code, and I believe that is good enough to submit. At the moment turning is proving to be a big challenge, so once I am finished that there will be a lot of updates to write.

<br>

Now that a submittable draft of the code is done, I will keep working on improving the firmware while my project gets (hopefully) approved and parts shipped out.

I created these diagrams to show how I will get the path of the robot, and then the path of it's wheels, in order

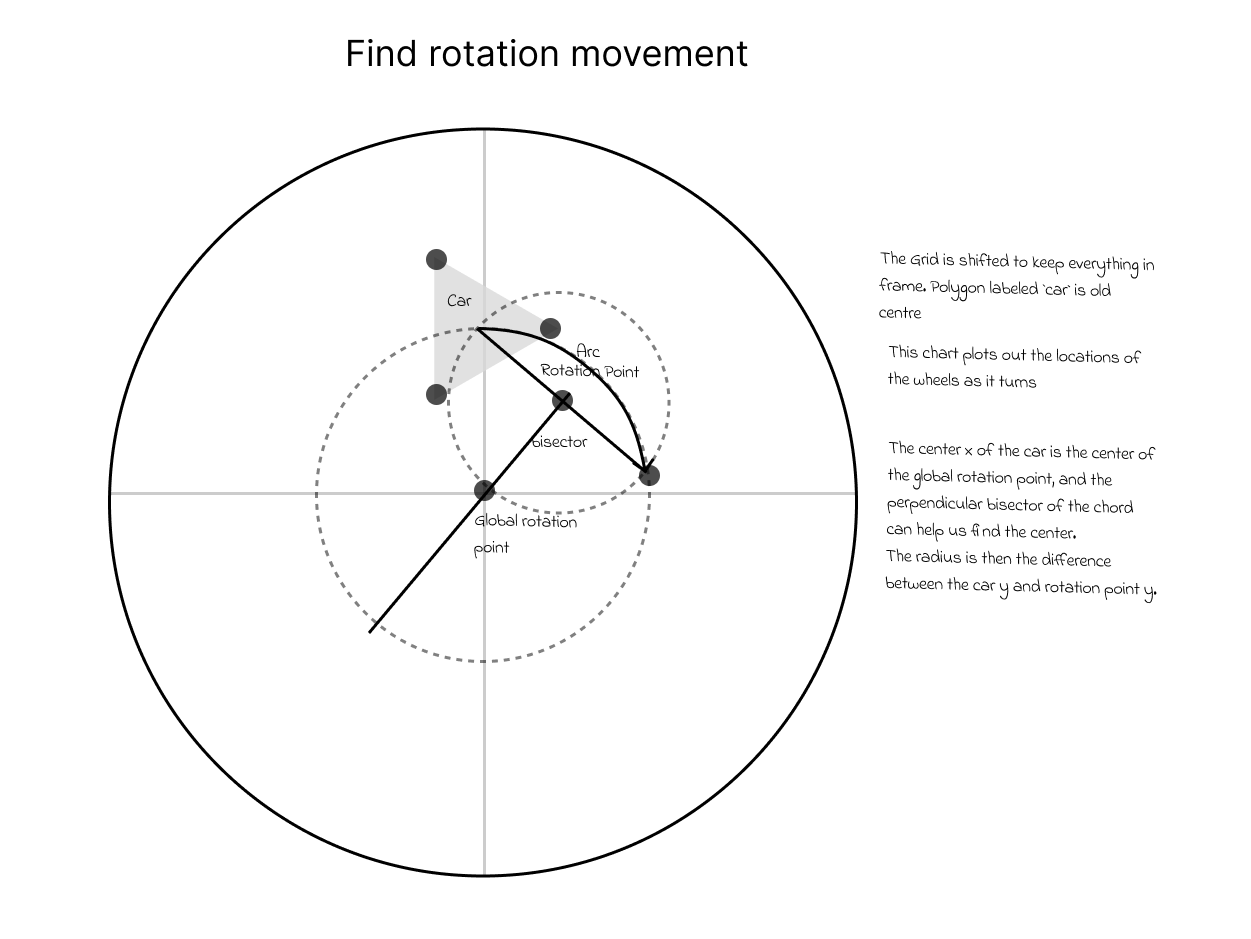
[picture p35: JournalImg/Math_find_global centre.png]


From here, I can use that global rotation circle to plot the movements of each individual wheel to try to distinguish a pattern

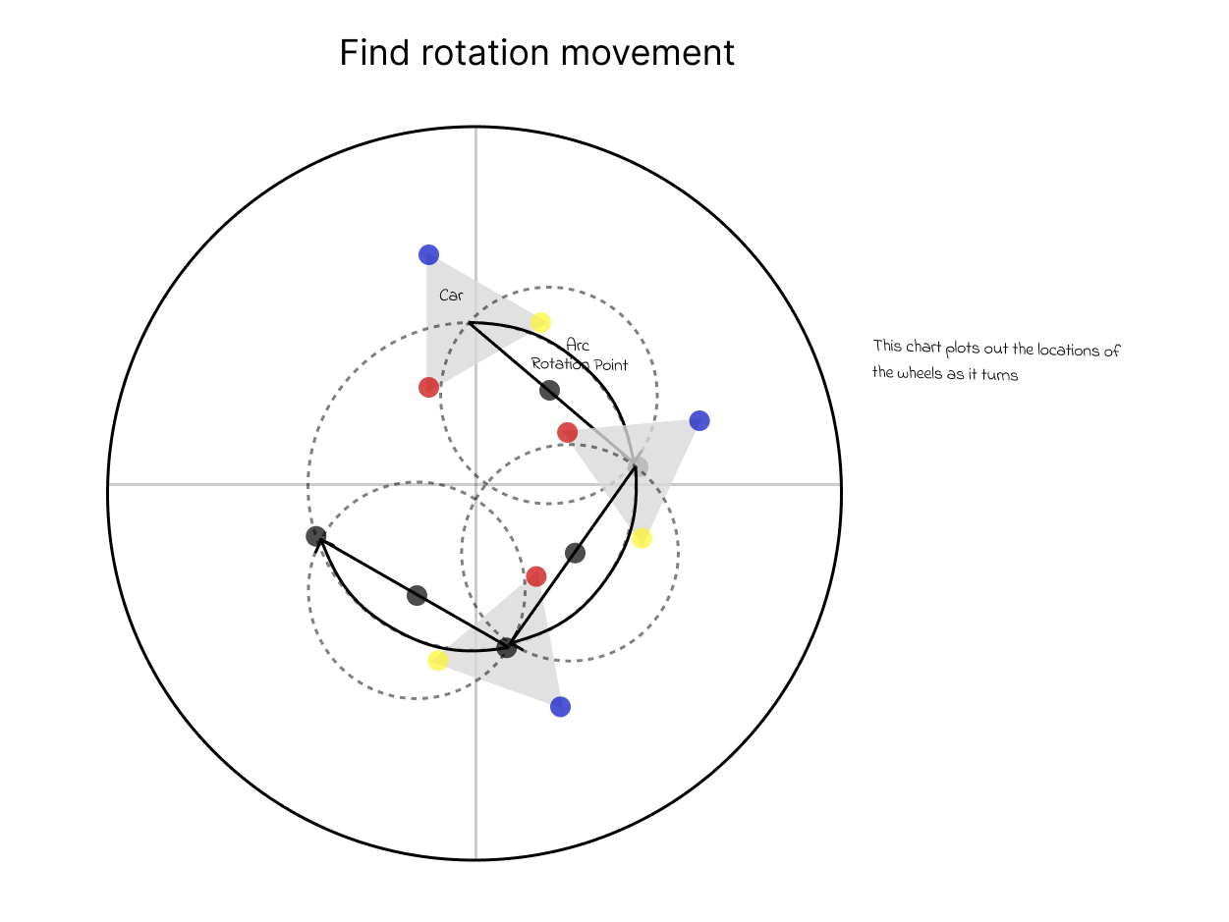
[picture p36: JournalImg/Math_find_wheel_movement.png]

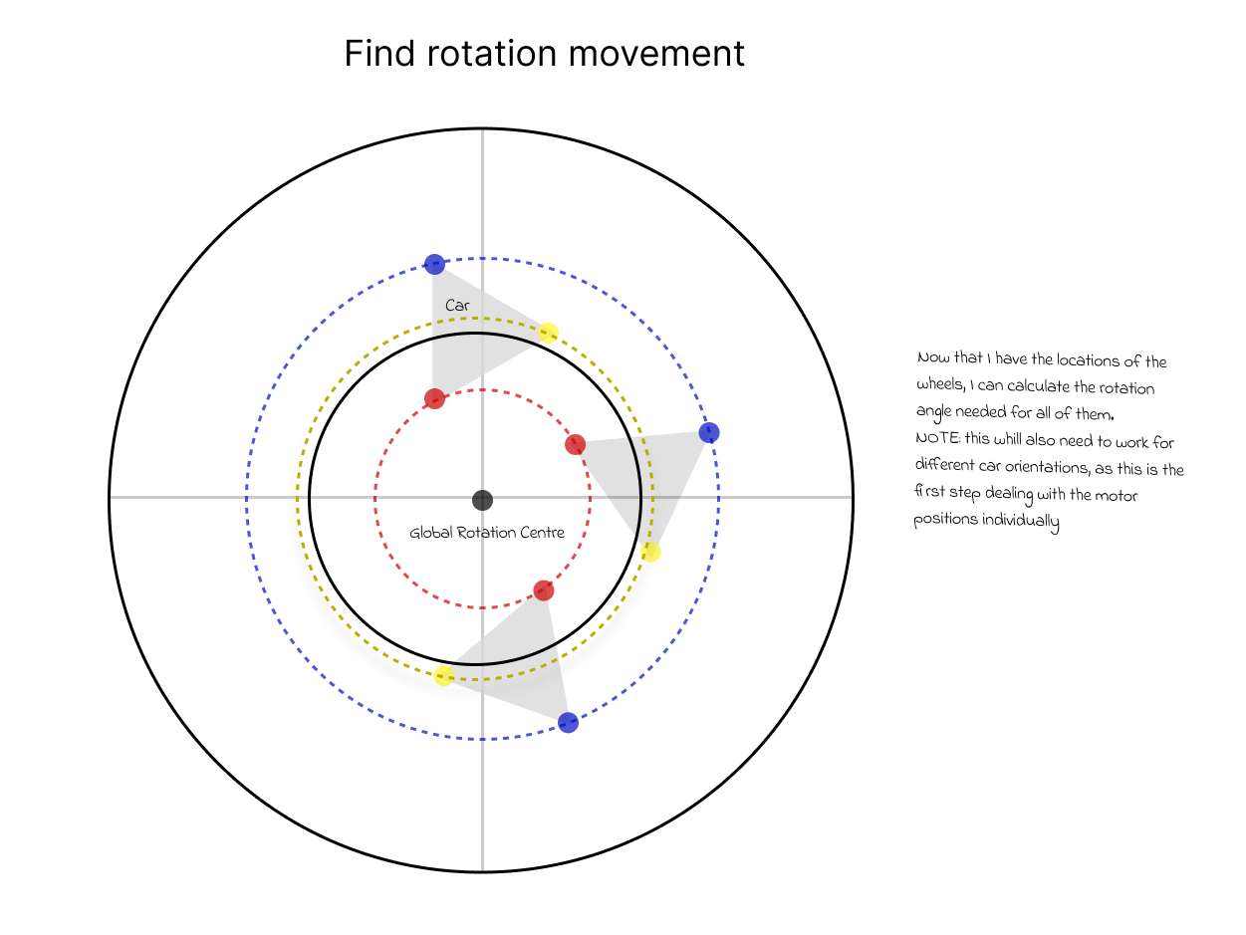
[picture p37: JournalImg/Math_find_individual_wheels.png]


So it turns out that each wheel rotates on its own circle around the same centre point, meaning that if I can isolate the modules and their circles, I can determine the angle needed for each of the modules and the speed of the motors.

**Total time spent: 5h**

# June 28th: Wayy more coding
I finished up the maths for Snake Drive (turning with crab) and am now working on coding it. Also I realized that I missed some stuff on the CAD so I will go back and fix that once am done.

I fixed all my snake drive code and it now uses the math shown above. Unfortunately until I build the robot I can't test or calibrate the firmware but I think it is a good starting point.

Time to fix the CAD

I realized that the wheels on the car are very exposed when they rotate outside of underneath the car, So my plan is to simply make a barrier that shields the outside of the motors without interfering too much with function.

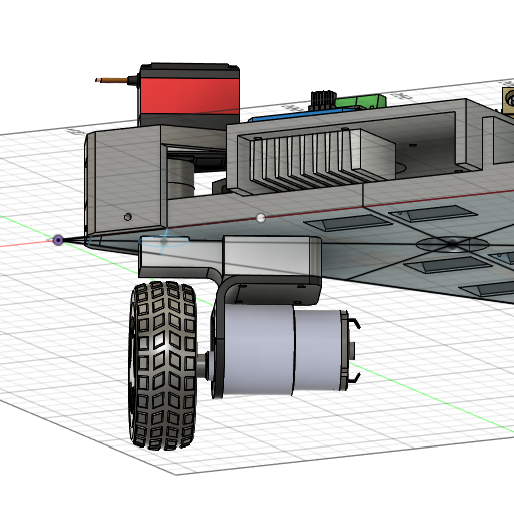
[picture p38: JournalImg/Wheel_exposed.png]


To make the shield, I created an expanded triangle around the base cut the corners a little, split it into one repeating piece (That I will need to print three times, because it is too big for my printer), and then added some screw holes to the base for attachment.

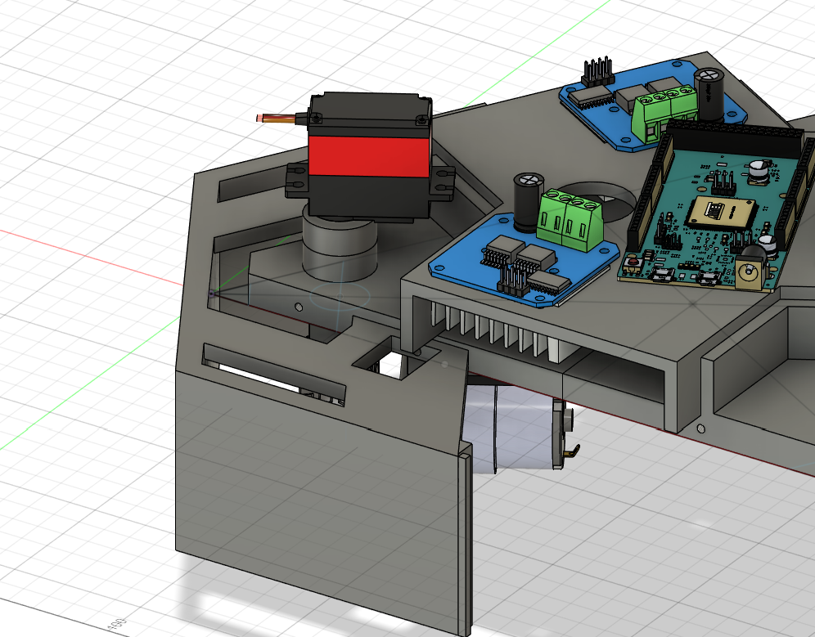
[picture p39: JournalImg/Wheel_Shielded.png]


<br>
<br>

5pm update: just spent around an hour figuring out a bunch of libraries to make the code a lot simpler, so that hopefully it will work first try. I also updated my BOM to be a lot cleaner and nicer.

**Total time spent:4h**

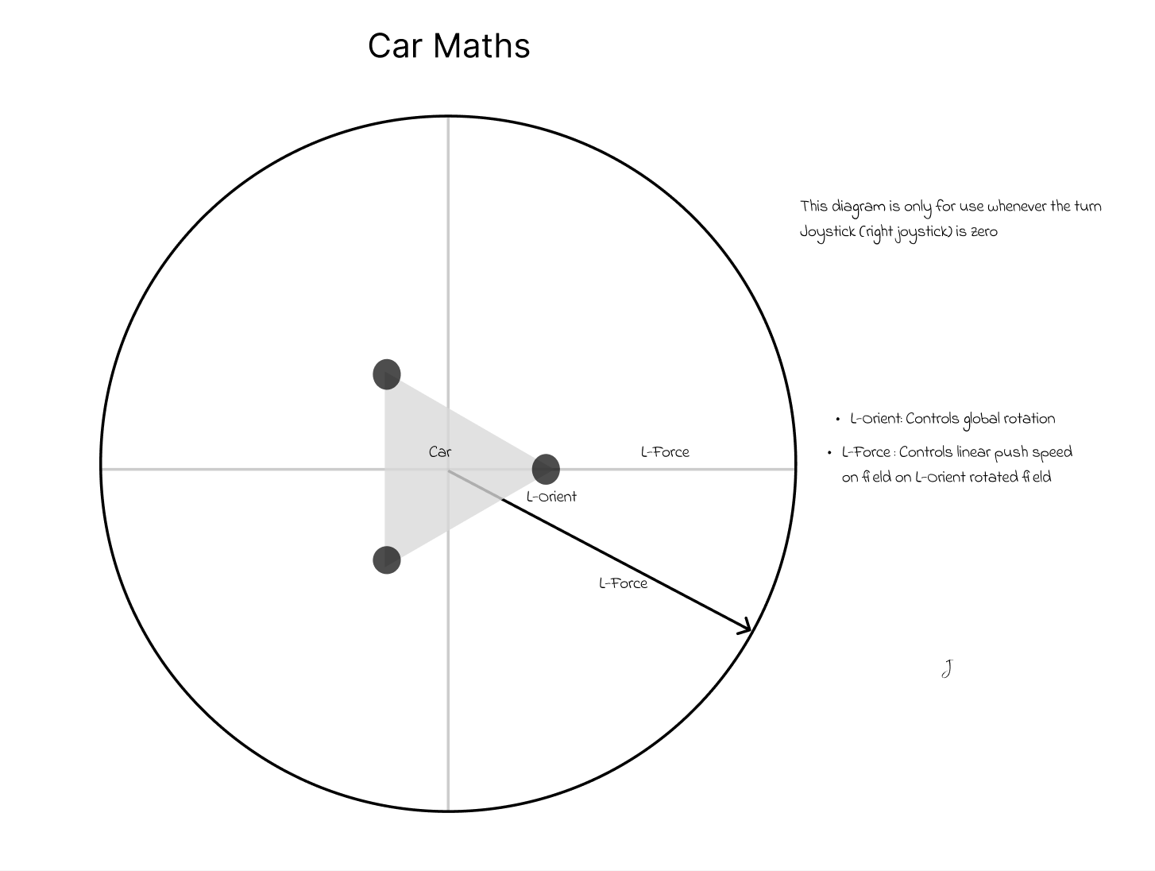
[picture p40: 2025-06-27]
JournalImg/Math_crab_drive_simple.png

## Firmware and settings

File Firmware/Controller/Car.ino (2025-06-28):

#include <Arduino.h>
#include <SPI.h>
#include <nRF24L01.h>
#include <RF24.h>
#include <stdio.h>
#include <printf.h>
#include <RF24_config.h>
#include <Servo.h>
using namespace std;

#define MessageID 45949




const int ServoPins[3] = {2,3,4};
//       Servos    1 2 3
const int ServoOffsets[3] = {0, 120, 240};

const uint8_t L_EN[3] = {30,32,34};
const uint8_t L_PWM[3] = {40,42,44};
const uint8_t R_EN[3] = {31,33,35};
const uint8_t R_PWM[3] = {41,43,45};
const uint8_t pushDistance = 512;
const float moduleDistance = 188.375;

int MotorSpeeds[3] = {0,0,0};
int ServoPositions[3] = {0, 0, 0};
Servo ServoObjects[3];


// Still need to do motor stuff


//Define structs
// This is how data is recieved from the controller
typedef struct{
  int16_t Identifier;
  float LeftJoyForce; // How far from center the joystick is
  float LeftJoyOrient; // The angle relative to the centre of the joystick
  float RightJoyForce;
  float RightJoyOrient;
}__attribute__((packed)) DataStruct;
DataStruct dataPackage;


typedef struct Point {
    float x, y;
};

// Define functions
Point lineIntersect(Point A, Point B, Point C, Point D);
void getModuleCrab(int (&Mos)[3], int (&Svp)[3]);
void getModuleSnake(int (&Mos)[3], int(&Svp)[3]);
float tangentAngleToXAxis(Point Centre, Point TanPoint);






// Define radio
RF24 radio(48,49); // CE, CSN
const byte address[5] = "0110";



void setup() {
  printf_begin();
  pinMode(48,  OUTPUT); 
  pinMode(49, OUTPUT);


  // attach servos to pins
  for (int i = 0; i < 3; i++){
    ServoObjects[i].attach(ServoPins[i]);
    pinMode(L_EN[i],  OUTPUT); 
    pinMode(R_EN[i],  OUTPUT); 
    pinMode(L_PWM[i],  OUTPUT); 
    pinMode(R_PWM[i],  OUTPUT);
  }

  // end pinmodes

  Serial.begin(9600); 
  if (!radio.begin()) { Serial.println(F("radio hardware not responding!"));}
  radio.openReadingPipe(0, address);
  radio.setPALevel(-18);
  radio.startListening();

  // Make an LED or something to check if Radio is transmitting
}






void loop() {
  while (!radio.available()); // If the radio drops out repeatedly i'll add the code for a restart then
  radio.read( &dataPackage, sizeof(DataStruct) );

  if (dataPackage.Identifier != MessageID){ // If unauthorized message
    return;
  };

  if (dataPackage.RightJoyForce == 0){ // if not turning, I want the simpler crab drive math to work
    getModuleCrab(MotorSpeeds, ServoPositions);
  } else {
    // I want it to reset until I get snake working
    // Once the complicated snake math is working, it goes here
    getModuleDefaults(MotorSpeeds, ServoPositions);
  }

  //I will need to figure out how to get the servo positioning to work
  for (int i = 0; i < 3; i++){
    
    int rotation = ServoPositions[i] - ServoOffsets[i];
    rotation = (rotation % 360);
    int ms = round(MotorSpeeds[i]/pushDistance*256);
    if (rotation < 180){
      analogWrite(L_PWM[i], 0);
      digitalWrite(L_EN[i], LOW);
      digitalWrite(R_EN[i], HIGH);
      analogWrite(R_PWM[i], ms);
      ServoObjects[i].write(rotation);


    } else {
      analogWrite(R_PWM[i], 0);
      digitalWrite(R_EN[i], LOW);
      analogWrite(L_PWM[i], ms);
      digitalWrite(L_EN[i], HIGH);
      ServoObjects[i].write(rotation - 180);
    }
  }
  
}








void getModuleCrab(int (&Mos)[3], int(&Svp)[3]) {
   // crab drive math; point and go
  for (int i = 0; i<3; i++){
    Mos[i] = round(dataPackage.LeftJoyForce); // still on the 512 scale NEED FIX
    Svp[i] = round(degrees(dataPackage.LeftJoyOrient));
  }
}


void getModuleSnake(int (&Mos)[3], int(&Svp)[3]){
   // Find rotation centre
    // Define vars
   int L_Orient = dataPackage.LeftJoyOrient;
   int R_Orient = dataPackage.RightJoyOrient + L_Orient; // rotate R_orient with L_orient
   int L_Force = dataPackage.LeftJoyForce;
   int R_Force = dataPackage.RightJoyForce;
   
   // Find the length of the vector
   int Vector_Hyp = L_Force - R_Force;
   
   Point Centre{0,0};
   // Find chord midpoint first
   // Don't even need to find chord first this vector is the midpoint
   float Vector_X = Vector_Hyp * cos(R_Orient);
   float Vector_Y = Vector_Hyp * sin(R_Orient);
   Point Midpoint{Vector_X, Vector_Y};
   // find any point on perpendicular bisector
   float Bisector_Slope = -(Midpoint.x - Centre.x)/(Midpoint.y-Centre.y);
   float Bisector_X = 513;
   float Bisector_Y_Intercept = Midpoint.y-(Midpoint.x * Bisector_Slope);
   float Bisector_Y = Bisector_Slope * Bisector_X + Bisector_Y_Intercept;
   Point ArbitraryBisectorSlope{Bisector_X, Bisector_Y};



   float Vector_X = Vector_Hyp * cos(L_Orient);
   float Vector_Y = Vector_Hyp * sin(L_Orient);
   Point AbitraryCenterLine{Vector_X,Vector_Y};

   // Rotation centre here
   Point Global_Rot_Center = lineIntersect(Centre, AbitraryCenterLine, Midpoint, ArbitraryBisectorSlope);
   
   // Now to find servo positions and motor speeds

   // Calculate motor speeds is after servo pos because we need the max
   float Radii[3] = {0,0,0};
   float Max_Rad = 0;
   for (int i = 0; i <3; i++){
      float Mdist = moduleDistance;
      // find the x/y of the motor
      int angle = radians(ServoOffsets[i]);
      float Vector_X = Mdist * cos(angle);
      float Vector_Y = Mdist * sin(angle);

      Point Module_Loc{Vector_X, Vector_Y};
      float Circle_rad = hypot(Module_Loc.x-Global_Rot_Center.x, Module_Loc.y-Global_Rot_Center.y);
      float angle = tangentAngleToXAxis(Global_Rot_Center,Module_Loc);

      Svp[i] = round(degrees(angle));
      Radii[i] = Circle_rad;
      if (Circle_rad > Max_Rad){
        Max_Rad = Circle_rad;
      }

    }

    for (int i=0; i< 3; i++){
      // Speed is on scale of 0 to 512
      float Speed_factor = Radii[i] / Max_Rad;
      Mos[i] = Speed_factor * pushDistance;

    }



}



void getModuleDefaults(int (&Mos)[3], int(&Svp)[3]) {
  // Resets motor speeds and all to defaults
  for (int i = 0; i<3; i++){
    Mos[i] = 0;
    Svp[i] = ServoOffsets[i];
  }
}

Point lineIntersect(Point A, Point B, Point C, Point D){
    float a1 = B.y - A.y;
    float b1 = A.x - B.x;
    float c1 = a1 * A.x + b1 * A.y;

    float a2 = D.y - C.y;
    float b2 = C.x - D.x;
    float c2 = a2 * C.x + b2 * C.y;

    float determinant = a1 * b2 - a2 * b1;

    if (determinant == 0) {
        return Point{0,0};
    } else {
        float x = (b2 * c1 - b1 * c2) / determinant;
        float y = (a1 * c2 - a2 * c1) / determinant;
        return Point{x, y};
    }
}


float tangentAngleToXAxis(Point Centre, Point TanPoint) {
    // Find slope of rad
    float radius_slope = (TanPoint.y - Centre.y) / (TanPoint.x - Centre.x);
    
    // Calculate the slope of the tangent line
    float m_tangent = -1 / radius_slope;  // Perpendicular slope
    
    //Calc tangent
    float angle_radians = atan(m_tangent);  // atan returns angle in radians
    
    return angle_radians; 
}

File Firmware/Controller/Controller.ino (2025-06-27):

#include <Arduino.h>
#include <SPI.h>
#include <nRF24L01.h>
#include <RF24.h>
#include <stdio.h>
#include <printf.h>
#include <RF24_config.h>
#include <BTS7960.h>
using namespace std;

#define LeftJoyX A0
#define LeftJoyY A1
#define RightJoyX A2
#define RightJoyY A3
#define MessageID 45949
#define ControlDeadZone 10

typedef struct{
  int16_t Identifier;
  float LeftJoyForce; // How far from center the joystick is
  float LeftJoyOrient; // The angle relative to the centre of the joystick
  float RightJoyForce;
  float RightJoyOrient;
}__attribute__((packed)) DataStruct;

DataStruct dataPackage;

RF24 radio(49,48); // CE, CSN CHANGE THESE PINS
// SPI PINS
// SCK: 52
// MO: 51
// MI: 50

//Vars

//Inputs
int leftX = 512;
int leftY = 512;
int rightX = 512;
int rightY = 512;
int VX = 0;
int VY = 0;
int OX = 512;
int OY = 512;
float force = 0;
//End vars


const byte address[5] = "0110";

void setup() {
  // pinmodes
  printf_begin();
  pinMode(48,  OUTPUT); 
  pinMode(49, OUTPUT);
  // end pinmodes

  Serial.begin(9600); 
  if (!radio.begin()) { Serial.println(F("radio hardware not responding!"));}
  radio.openReadingPipe(0, address);
  radio.setPALevel(-18);
  radio.stopListening();

  // Make an LED or something to check if Radio is transmitting
  dataPackage.Identifier = MessageID;
}



void loop() {
  leftX = analogRead(LeftJoyX);
  leftY = analogRead(LeftJoyY);
  rightX = analogRead(RightJoyX);
  rightY = analogRead(RightJoyY);
  // put your main code here, to run repeatedly:
  
  //left side
  VX = leftX - OX;
  VY = leftY - OY;
  force = sqrt(pow(VX, 2) + pow(VY, 2));
  if (force < ControlDeadZone){
    dataPackage.RightJoyForce = 0;
    dataPackage.LeftJoyOrient = 0;
  } else {
    dataPackage.LeftJoyForce = sqrt(force);
    dataPackage.LeftJoyOrient = atan2(VX,VY);
  }
  

  VX = rightX - OX;
  VY = rightY - OY;
  force = sqrt(pow(VX, 2) + pow(VY, 2));
  if (force < ControlDeadZone){
    dataPackage.RightJoyForce = 0;
    dataPackage.RightJoyOrient = 0;
  } else {
    dataPackage.RightJoyForce = sqrt(force);
    dataPackage.RightJoyOrient = atan2(VX,VY);
  }


  radio.write(&dataPackage, sizeof(DataStruct));
  delay(10);


}

// for the cars code, I want the turning to set a point outside the car to turn around. The turning itself will be a constant value, however it will have a perception of distance by the force vector and the turn force
// I can finish this while parts arrive

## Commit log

2025-06-24 commit June 9th
    [Body.3mf]
2025-06-25 Add CAD stuff
    [Body.3mf, Body1.3mf, Half 1.3mf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]
2025-06-26 Commit June 25th I have no idea what the hell I was thinking with those other dates on the commits my brain was half a month off
    [Body1.3mf, Circuit diagram.fzz, Half 1.3mf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]
2025-06-26 restructure files
    [Body1.3mf, Circuit diagram.fzz, Half 1.3mf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]
2025-06-26 add screwholes to CAD
    [Half 1.3mf, Half 2.3mf]
2025-06-26 Finish controller CAD
    [Controller.step]
2025-06-26 Finish circuits
    [Car diagram.fzz, Controller diagram.fzz]
2025-06-26 Reorganize file and add production files
    [Body Top.3mf, Body1.3mf, Controller Top.3mf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]
2025-06-26 Add car cad expanded
2025-06-26 go back
    [BOM.csv]
2025-06-26 hopefully done there
    [BOM.csv]
2025-06-26 Switch Due with Mega
    [BOM.csv]
2025-06-27 start more software
    [Car diagram.fzz]
2025-06-28 add shield for CAD
    [Half 1.3mf, Half 2.3mf, Motor Shield.3mf]
2025-06-28 rename files even though vscode gives me an error and i hate it so much why why why why whyw hy
    [Car.ino, Controller.ino]
2025-06-28 update BOM
    [BOM.csv]
2025-06-28 update BOM / readme
    [BOM.csv]
2025-06-29 update CAD
    [Half 1.3mf, Half 2.3mf]
2025-06-30 fix CAD + explain power
